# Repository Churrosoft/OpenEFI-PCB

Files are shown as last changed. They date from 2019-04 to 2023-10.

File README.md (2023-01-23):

# OpenEFI-PCB
Coleccion de PCB y planos recomendados para montar una OpenEFI

### Sobre el proyecto
OpenEFI es un ECU/EFI programable basada en arduino, totalmente OpenSource, fue creada originalmente para reemplazar una ecu existente en un motor naftero, pero tambien se puede usar para agregar inyeccion y/o encendido electronico a un motor antiguo, cuenta tambien con soporte para DTC's y autodiagnostico
* [OpenEFI](https://github.com/FDSoftware/OpenEFI) [Repo principal con todo el codigo]
* [OpenEFI-Tuner](https://github.com/FDSoftware/OpenEFI-Tuner) [Utilidad para revisar el estado de la ecu y modificarla]
* 
### Placas soportadas
* STM32F407xxxx: uEFI (v2/v3)
* STM32F103c8t6: OpenEFI (v0.5/v1/v2)

### coautores externos:
Dibujos:
Lucacik / ig: https://www.instagram.com/luca.cik/

si quieres usar otra placa basada en Arduino (Uno, Mega,DUE,etc), puedes hacerlo, pero los pcb no te serviran y capaz tengas que modificar ligeramente el codigo y el mapeo de los pines, proximamente agregare mas pcb ademas de mejorar los existentes

This source is distributed WITHOUT ANY EXPRESS OR IMPLIED WARRANTY, INCLUDING OF MERCHANTABILITY, SATISFACTORY QUALITY AND FITNESS FOR A PARTICULAR PURPOSE.

Please see LICENSE file for applicable conditions.

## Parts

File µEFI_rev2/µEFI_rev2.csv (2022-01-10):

Source: | /home/fdsoftware/repos/churrosoft/OpenEFI-PCB/µEFI_rev2/µEFI_rev2.kicad_sch
Date: | mar 05 oct 2021 17:01:05
Tool: | Eeschema (5.99.0-12387-g847c9e32c8)
Generator: | /usr/share/kicad-nightly/plugins/bom_csv_grouped_by_value.py
Component Count: | 171
Individual Components:
Item | Qty | Reference(s) | Value | LibPart | Footprint | Datasheet | Availability | DIGY | Description | Field4 | Field5 | Field6 | Field7 | Height | LCSC | MF | MP | Manufacturer_Name | Manufacturer_Part_Number | Mouser Part Number | Mouser Price/Stock | Note | Package | Price | STOCK
 |  | C2 | 15pF | Device:C_Small | Capacitor_SMD:C_0805_2012Metric | ~ |  |  |  |  |  |  |  |  | C1794
 |  | C3 | 15pF | Device:C_Small | Capacitor_SMD:C_0805_2012Metric | ~ |  |  |  |  |  |  |  |  | C1794
 |  | C5 | 100nF | Device:C_Small | Capacitor_SMD:C_0805_2012Metric | ~ |  |  |  |  |  |  |  |  | C49678
 |  | C6 | 1uF | Device:C_Small | Capacitor_SMD:C_0805_2012Metric | ~ |  |  |  |  |  |  |  |  | C28323
 |  | C7 | 2.2uF | Device:C_Small | Capacitor_SMD:C_0805_2012Metric | ~ |  |  |  |  |  |  |  |  | C49217 |  |  |  |  |  |  | Low ESR <2Ohm
 |  | C8 | 2.2uF | Device:C_Small | Capacitor_SMD:C_0805_2012Metric | ~ |  |  |  |  |  |  |  |  | C49217 |  |  |  |  |  |  | Low ESR <2Ohm
 |  | C9 | 100nF | Device:C_Small | Capacitor_SMD:C_0805_2012Metric | ~ |  |  |  |  |  |  |  |  | C49678
 |  | C10 | 100nF | Device:C_Small | Capacitor_SMD:C_0805_2012Metric | ~ |  |  |  |  |  |  |  |  | C49678
 |  | C11 | 100nF | Device:C_Small | Capacitor_SMD:C_0805_2012Metric | ~ |  |  |  |  |  |  |  |  | C49678
 |  | C12 | 100nF | Device:C_Small | Capacitor_SMD:C_0805_2012Metric | ~ |  |  |  |  |  |  |  |  | C49678
 |  | C13 | 100nF | Device:C_Small | Capacitor_SMD:C_0805_2012Metric | ~ |  |  |  |  |  |  |  |  | C49678
 |  | C14 | 100nF | Device:C_Small | Capacitor_SMD:C_0805_2012Metric | ~ |  |  |  |  |  |  |  |  | C49678
 |  | C15 | 100nF | Device:C_Small | Capacitor_SMD:C_0805_2012Metric | ~ |  |  |  |  |  |  |  |  | C49678
 |  | C16 | 4.7uF | Device:CP_Small | Capacitor_SMD:C_0805_2012Metric | ~ |  |  |  |  |  |  |  |  | 0805
 |  | C17 | 100nF | Device:C_Small | Capacitor_SMD:C_0805_2012Metric | ~ |  |  |  |  |  |  |  |  | C49678
 |  | C18 | 10pF | Device:C_Small | Capacitor_SMD:C_0603_1608Metric | ~ |  |  |  |  |  |  |  |  | C106245
 |  | C19 | 10pF | Device:C_Small | Capacitor_SMD:C_0603_1608Metric | ~ |  |  |  |  |  |  |  |  | C106245
 |  | C20 | 10pF | Device:C_Small | Capacitor_SMD:C_0603_1608Metric | ~ |  |  |  |  |  |  |  |  | C106245
 |  | C21 | 10pF | Device:C_Small | Capacitor_SMD:C_0603_1608Metric | ~ |  |  |  |  |  |  |  |  | C106245
 |  | C22 | 10pF | Device:C_Small | Capacitor_SMD:C_0603_1608Metric | ~
 |  | C23 | 10nF | Device:C_Small | Capacitor_SMD:C_0603_1608Metric | ~ |  |  |  |  |  |  |  |  | C100042
 |  | C24 | 10nF | Device:C_Small | Capacitor_SMD:C_0603_1608Metric | ~ |  |  |  |  |  |  |  |  | C100042
 |  | C25 | 10nF | Device:C_Small | Capacitor_SMD:C_0603_1608Metric | ~ |  |  |  |  |  |  |  |  | C100042
 |  | C26 | 10nF | Device:C_Small | Capacitor_SMD:C_0603_1608Metric | ~ |  |  |  |  |  |  |  |  | C100042
 |  | C27 | 10nF | Device:C_Small | Capacitor_SMD:C_0603_1608Metric | ~ |  |  |  |  |  |  |  |  | C100042
 |  | C28 | 10nF | Device:C_Small | Capacitor_SMD:C_0603_1608Metric | ~ |  |  |  |  |  |  |  |  | C100042
 |  | C29 | 10nF | Device:C_Small | Capacitor_SMD:C_0603_1608Metric | ~ |  |  |  |  |  |  |  |  | C100042
 |  | C30 | 10nF | Device:C_Small | Capacitor_SMD:C_0603_1608Metric | ~ |  |  |  |  |  |  |  |  | C100042
 |  | C31 | 100uF ±20% 35V | Device:CP_Small | Capacitor_SMD:CP_Elec_6.3x7.7 | ~ |  |  |  |  |  |  |  |  | C141427
 |  | C33 | 47nF | Device:C_Small | Capacitor_SMD:C_0603_1608Metric | ~
 |  | C34 | 4.7nF | Device:C_Small | Capacitor_SMD:C_0805_2012Metric | ~ |  |  |  |  |  |  |  |  | C77475
 |  | C36 | 0.1uF | Device:C_Small | Capacitor_SMD:C_0603_1608Metric | ~
 |  | C49 | 240pF | Device:C_Small | Capacitor_SMD:C_0603_1608Metric | ~ |  |  |  |  |  |  |  |  | C185593
 |  | C51 | 240pF | Device:C_Small | Capacitor_SMD:C_0603_1608Metric | ~ |  |  |  |  |  |  |  |  | C185593
 |  | C52 | 0.01uF | Device:C_Small | Capacitor_SMD:C_0603_1608Metric | ~ |  |  |  |  |  |  |  |  | C100042
 |  | C53 | 0.01uF | Device:C_Small | Capacitor_SMD:C_0603_1608Metric | ~ |  |  |  |  |  |  |  |  | C100042
 |  | C54 | 0.01uF | Device:C_Small | Capacitor_SMD:C_0603_1608Metric | ~ |  |  |  |  |  |  |  |  | C100042
 |  | C55 | 0.01uF | Device:C_Small | Capacitor_SMD:C_0603_1608Metric | ~ |  |  |  |  |  |  |  |  | C100042
 |  | C56 | 0.01uF | Device:C_Small | Capacitor_SMD:C_0603_1608Metric | ~ |  |  |  |  |  |  |  |  | C100042
 |  | C57 | 0.01uF | Device:C_Small | Capacitor_SMD:C_0603_1608Metric | ~ |  |  |  |  |  |  |  |  | C100042
 |  | D1 | LED | Device:LED | LED_SMD:LED_0603_1608Metric | ~
 |  | D2 | 1N4148 | Diode:1N4148 | Diode_SMD:D_SOD-523 | https://assets.nexperia.com/documents/data-sheet/1N4148_1N4448.pdf |  |  |  |  |  |  |  |  | C511874
 |  | D3 | 1N4148 | Diode:1N4148 | Diode_SMD:D_SOD-523 | https://assets.nexperia.com/documents/data-sheet/1N4148_1N4448.pdf |  |  |  |  |  |  |  |  | C511874
 |  | D4 | SMAJ58CA | Device:D_TVS | Diode_SMD:D_SMA | ~
 |  | D5 | LED | Device:LED | LED_SMD:LED_0603_1608Metric | ~
 |  | D6 | LED | Device:LED | LED_SMD:LED_0603_1608Metric | ~
 |  | D7 | LED | Device:LED | LED_SMD:LED_0603_1608Metric | ~
 |  | D8 | LED | Device:LED | LED_SMD:LED_0603_1608Metric | ~
 |  | D9 | LED | Device:LED | LED_SMD:LED_0603_1608Metric | ~
 |  | D10 | LED | Device:LED | LED_SMD:LED_0603_1608Metric | ~
 |  | D11 | MM3Z24VT1G | Device:D_Zener | Diode_SMD:D_SOD-323 | ~ |  |  |  |  |  |  |  |  |  |  |  |  |  |  |  |  |  |  | BI000000597
 |  | D12 | LED | Device:LED | LED_SMD:LED_0603_1608Metric | ~
 |  | D13 | LED | Device:LED | LED_SMD:LED_0603_1608Metric | ~
 |  | D14 | DZ2S033X0L | :Diode:DZ2S033X0L_1 | Diode_SMD:D_MiniMELF | https://industrial.panasonic.com/content/data/SC/ds/ds4/DZ2S03300L_E.pdf |  |  |  |  |  |  |  |  | C8056
 |  | D18 | DZ2S033X0L | Diode:DZ2S033X0L | Diode_SMD:D_MiniMELF | https://industrial.panasonic.com/content/data/SC/ds/ds4/DZ2S03300L_E.pdf |  |  |  |  |  |  |  |  | C8056
 |  | H1 | MountingHole | Mechanical:MountingHole | MountingHole:MountingHole_2.2mm_M2_Pad_Via | ~
 |  | H2 | MountingHole | Mechanical:MountingHole | MountingHole:MountingHole_2.2mm_M2_Pad_Via | ~
 |  | H3 | MountingHole | Mechanical:MountingHole | MountingHole:MountingHole_2.2mm_M2_Pad_Via | ~
 |  | H4 | MountingHole | Mechanical:MountingHole | MountingHole:MountingHole_2.2mm_M2_Pad_Via | ~
 |  | H5 | MountingHole | Mechanical:MountingHole | TestPoint:TestPoint_Pad_D1.0mm | ~
 |  | H6 | MountingHole | Mechanical:MountingHole | TestPoint:TestPoint_Pad_D1.0mm | ~
 |  | H7 | MountingHole | Mechanical:MountingHole | TestPoint:TestPoint_Pad_D1.0mm | ~
 |  | H8 | MountingHole | Mechanical:MountingHole | TestPoint:TestPoint_Pad_D1.0mm | ~
 |  | H9 | MountingHole | Mechanical:MountingHole | MountingHole:MountingHole_2.2mm_M2_Pad_Via | ~
 |  | J1 | USB_B | STM32F_rev3-rescue:USB_B-Connector | Connector_USB:USB_B_OST_USB-B1HSxx_Horizontal | ~
 |  | J2 | Tag connect | Connector_Generic:Conn_02x03_Odd_Even | Connector:Tag-Connect_TC2030-IDC-NL_2x03_P1.27mm_Vertical | ~
 |  | J3 | 36638-0002 | OpenEFI-STM32-rev3:36638-0002 | 366380002 | https://www.molex.com/webdocs/datasheets/pdf/en-us/0366380002_PCB_HEADERS.pdf |  |  | MOLEX - 36638-0002 - HEADER, CMC, SINGLE PORT, R/A, 48WAY |  |  |  |  | 30 |  |  |  | Molex | 36638-0002 | 538-36638-0002 | https://www.mouser.co.uk/ProductDetail/Molex/36638-0002?qs=xXuHO2M8Escly3rEMcmzyw%3D%3D
 |  | J4 | Conn_02x08_Odd_Even | Connector_Generic:Conn_02x08_Odd_Even | Connector_PinHeader_1.27mm:PinHeader_2x08_P1.27mm_Vertical | ~
 |  | JP1 | SolderJumper_2_Open | Jumper:SolderJumper_2_Open | Jumper:SolderJumper-2_P1.3mm_Open_RoundedPad1.0x1.5mm | ~
 |  | JP2 | SolderJumper_2_Open | Jumper:SolderJumper_2_Open | Jumper:SolderJumper-2_P1.3mm_Open_RoundedPad1.0x1.5mm | ~
 |  | JP3 | SolderJumper_2_Open | Jumper:SolderJumper_2_Open | Jumper:SolderJumper-2_P1.3mm_Open_RoundedPad1.0x1.5mm | ~
 |  | JP4 | Jumper_NO_Small | Device:Jumper_NO_Small | Jumper:SolderJumper-2_P1.3mm_Open_RoundedPad1.0x1.5mm | ~
 |  | JP11 | Jumper_NC_Small | Device:Jumper_NC_Small | Jumper:SolderJumper-2_P1.3mm_Open_TrianglePad1.0x1.5mm | ~
 |  | JP15 | Jumper_NC_Small | Device:Jumper_NC_Small | Jumper:SolderJumper-2_P1.3mm_Open_TrianglePad1.0x1.5mm | ~
 |  | JP17 | Jumper_NC_Small | Device:Jumper_NC_Small | Jumper:SolderJumper-2_P1.3mm_Open_TrianglePad1.0x1.5mm | ~
 |  | JP18 | Jumper_NC_Small | Device:Jumper_NC_Small | Jumper:SolderJumper-2_P1.3mm_Open_TrianglePad1.0x1.5mm | ~
 |  | JP19 | Jumper_NC_Small | Device:Jumper_NC_Small | Jumper:SolderJumper-2_P1.3mm_Open_TrianglePad1.0x1.5mm | ~
 |  | JP23 | SolderJumper_2_Open | Jumper:SolderJumper_2_Open | Jumper:SolderJumper-2_P1.3mm_Open_RoundedPad1.0x1.5mm | ~
 |  | JP24 | SolderJumper_2_Open | Jumper:SolderJumper_2_Open | Jumper:SolderJumper-2_P1.3mm_Open_RoundedPad1.0x1.5mm | ~
 |  | LOGO1 | Logo_Open_Hardware_Large | Graphic:Logo_Open_Hardware_Large | Symbol:OSHW-Logo2_14.6x12mm_SilkScreen | ~
 |  | Q1 | ISL9V5045S3ST | Device:Q_NIGBT_GCE | Package_TO_SOT_SMD:TO-263-2 | ~
 |  | Q2 | ISL9V5045S3ST | Device:Q_NIGBT_GCE | Package_TO_SOT_SMD:TO-263-2 | ~
 |  | Q3 | ISL9V5045S3ST | Device:Q_NIGBT_GCE | Package_TO_SOT_SMD:TO-263-2 | ~
 |  | Q4 | ISL9V5045S3ST | Device:Q_NIGBT_GCE | Package_TO_SOT_SMD:TO-263-2 | ~
 |  | Q5 | SS8050 | Transistor_BJT:2N3055 | Package_TO_SOT_SMD:SOT-23 | http://www.onsemi.com/pub_link/Collateral/2N3055-D.PDF |  |  |  |  |  |  |  |  | C2150
 |  | Q6 | IRF540N | :Transistor_FET:IRF540N_1 | Package_TO_SOT_THT:TO-220-3_Vertical | http://www.irf.com/product-info/datasheets/data/irf540n.pdf
 |  | Q7 | IRF540N | :Transistor_FET:IRF540N_2 | Package_TO_SOT_THT:TO-220-3_Vertical | http://www.irf.com/product-info/datasheets/data/irf540n.pdf
 |  | Q8 | SS8050 | Transistor_BJT:2N3055 | Package_TO_SOT_SMD:SOT-23 | http://www.onsemi.com/pub_link/Collateral/2N3055-D.PDF |  |  |  |  |  |  |  |  | C2150
 |  | Q9 | SS8050 | Transistor_BJT:2N3055 | Package_TO_SOT_SMD:SOT-23 | http://www.onsemi.com/pub_link/Collateral/2N3055-D.PDF |  |  |  |  |  |  |  |  | C2150
 |  | Q10 | IRF540N | Transistor_FET:IRF540N | Package_TO_SOT_THT:TO-220-3_Vertical | http://www.irf.com/product-info/datasheets/data/irf540n.pdf
 |  | Q11 | SS8050 | Transistor_BJT:2N3055 | Package_TO_SOT_SMD:SOT-23 | http://www.onsemi.com/pub_link/Collateral/2N3055-D.PDF |  |  |  |  |  |  |  |  | C2150
 |  | Q12 | AO3400A | Transistor_FET:AO3400A | Package_TO_SOT_SMD:SOT-23 | http://www.aosmd.com/pdfs/datasheet/AO3400A.pdf |  |  |  |  |  |  |  |  | C347475
 |  | R1 | R_Small | Device:R_Small | Resistor_SMD:R_1206_3216Metric | ~ |  |  |  |  |  |  |  |  | C205298
 |  | R2 | 10k | Device:R_Small | Resistor_SMD:R_0603_1608Metric | ~
 |  | R3 | 4.7k | Device:R_Small | Resistor_SMD:R_0603_1608Metric | ~ |  |  |  |  |  |  |  |  | C23162
 |  | R4 | 4.7k | Device:R_Small | Resistor_SMD:R_0603_1608Metric | ~ |  |  |  |  |  |  |  |  | C23162
 |  | R5 | 4.7k | Device:R_Small | Resistor_SMD:R_0603_1608Metric | ~ |  |  |  |  |  |  |  |  | C23162
 |  | R6 | 100R | Device:R_Small | Resistor_SMD:R_0603_1608Metric | ~ |  |  |  |  |  |  |  |  | C159890
 |  | R7 | 100R | Device:R_Small | Resistor_SMD:R_0603_1608Metric | ~ |  |  |  |  |  |  |  |  | C159890
 |  | R8 | 0.02R | Device:R_Small | Resistor_SMD:R_2512_6332Metric | ~ |  |  |  |  |  |  |  |  | C326611
 |  | R9 | 4.02k | Device:R_Small | Resistor_SMD:R_0603_1608Metric | ~ |  |  |  |  |  |  |  |  | C23040
 |  | R10 | 4.02k | Device:R_Small | Resistor_SMD:R_0603_1608Metric | ~ |  |  |  |  |  |  |  |  | C23040
 |  | R11 | 4.02k | Device:R_Small | Resistor_SMD:R_0603_1608Metric | ~ |  |  |  |  |  |  |  |  | C23040
 |  | R12 | 4.02k | Device:R_Small | Resistor_SMD:R_0603_1608Metric | ~ |  |  |  |  |  |  |  |  | C23040
 |  | R13 | 36K | Device:R_Small | Resistor_SMD:R_0603_1608Metric | ~ |  |  |  |  |  |  |  |  | C192548
 |  | R14 | 36K | Device:R_Small | Resistor_SMD:R_0603_1608Metric | ~ |  |  |  |  |  |  |  |  | C192548
 |  | R15 | 36K | Device:R_Small | Resistor_SMD:R_0603_1608Metric | ~ |  |  |  |  |  |  |  |  | C192548
 |  | R16 | 36K | Device:R_Small | Resistor_SMD:R_0603_1608Metric | ~ |  |  |  |  |  |  |  |  | C192548
 |  | R17 | 10K 1/10W | Device:R_Small | Resistor_SMD:R_0603_1608Metric | ~
 |  | R18 | 10R 1/10W | Device:R_Small | Resistor_SMD:R_0603_1608Metric | ~
 |  | R19 | 1M 1/10W | Device:R_Small | Resistor_SMD:R_0603_1608Metric | ~
 |  | R20 | 10R 1/10W | Device:R_Small | Resistor_SMD:R_0603_1608Metric | ~
 |  | R21 | 0.01R | Device:R_Small | Resistor_SMD:R_1210_3225Metric | ~ |  |  |  |  |  |  |  |  | C175884
 |  | R22 | 57.6K 1/10W | Device:R_Small | Resistor_SMD:R_0603_1608Metric | ~
 |  | R23 | 4.99K 1/10W | Device:R_Small | Resistor_SMD:R_0603_1608Metric | ~
 |  | R24 | 4.7k | Device:R_Small | Resistor_SMD:R_0603_1608Metric | ~ |  |  |  |  |  |  |  |  | C23162
 |  | R25 | 4.7k | Device:R_Small | Resistor_SMD:R_0603_1608Metric | ~ |  |  |  |  |  |  |  |  | C23162
 |  | R26 | 4.7k | Device:R_Small | Resistor_SMD:R_0603_1608Metric | ~ |  |  |  |  |  |  |  |  | C23162
 |  | R27 | 4.7k | Device:R_Small | Resistor_SMD:R_0603_1608Metric | ~ |  |  |  |  |  |  |  |  | C23162
 |  | R28 | R_Small | Device:R_Small | Resistor_SMD:R_1206_3216Metric | ~ |  |  |  |  |  |  |  |  | C205298
 |  | R29 | 4.7k | Device:R_Small | Resistor_SMD:R_0603_1608Metric | ~ |  |  |  |  |  |  |  |  | C23162
 |  | R30 | 4.7k | Device:R_Small | Resistor_SMD:R_0603_1608Metric | ~ |  |  |  |  |  |  |  |  | C23162
 |  | R31 | 1k | Device:R | Resistor_SMD:R_0603_1608Metric | ~ |  |  |  |  |  |  |  |  | C21190
 |  | R32 | 1k | Device:R | Resistor_SMD:R_0603_1608Metric | ~ |  |  |  |  |  |  |  |  | C21190
 |  | R33 | 10R 1/10W | Device:R_Small | Resistor_SMD:R_0603_1608Metric | ~
 |  | R34 | 1k | Device:R | Resistor_SMD:R_0603_1608Metric | ~ |  |  |  |  |  |  |  |  | C21190
 |  | R35 | 100k | Device:R | Resistor_SMD:R_0805_2012Metric | ~ |  |  |  |  |  |  |  |  | --- |  |  |  |  |  |  |  |  |  | 44
 |  | R81 | 4.99K 1/2W | Device:R_Small | Resistor_SMD:R_1210_3225Metric | ~ |  |  |  |  |  |  |  |  | C407178
 |  | R82 | 100k 1/10W +-1% | Device:R_Small | Resistor_SMD:R_0603_1608Metric | ~ |  |  |  |  |  |  |  |  | C217840
 |  | R83 | 20k 1/10W +-1% | Device:R_Small | Resistor_SMD:R_0603_1608Metric | ~
 |  | R87 | 3.32k +-1% | Device:R_Small | Resistor_SMD:R_0603_1608Metric | ~ |  |  |  |  |  |  |  |  | C234508
 |  | R92 | 28.6k +-1% | Device:R_Small | Resistor_SMD:R_0603_1608Metric | ~ |  |  |  |  |  |  |  |  | C217931
 |  | R97 | 2.2k | Device:R_Small | Resistor_SMD:R_0603_1608Metric | ~ |  |  |  |  |  |  |  |  | C309092
 |  | R108 | 10k | Device:R_Small | Resistor_SMD:R_0603_1608Metric | ~
 |  | R109 | 10k | Device:R_Small | Resistor_SMD:R_0603_1608Metric | ~
 |  | R112 | 4.99K 1/2W | Device:R_Small | Resistor_SMD:R_1210_3225Metric | ~ |  |  |  |  |  |  |  |  | C407178
 |  | R113 | 4.99K 1/2W | Device:R_Small | Resistor_SMD:R_1210_3225Metric | ~ |  |  |  |  |  |  |  |  | C407178
 |  | R114 | 4.99K 1/2W | Device:R_Small | Resistor_SMD:R_1210_3225Metric | ~ |  |  |  |  |  |  |  |  | C407178
 |  | R115 | 4.99K 1/2W | Device:R_Small | Resistor_SMD:R_1210_3225Metric | ~ |  |  |  |  |  |  |  |  | C407178
 |  | R116 | 4.99K 1/2W | Device:R_Small | Resistor_SMD:R_1210_3225Metric | ~ |  |  |  |  |  |  |  |  | C407178
 |  | R117 | 4.99K 1/2W | Device:R_Small | Resistor_SMD:R_1210_3225Metric | ~ |  |  |  |  |  |  |  |  | C407178
 |  | R118 | 4.99K 1/2W | Device:R_Small | Resistor_SMD:R_1210_3225Metric | ~ |  |  |  |  |  |  |  |  | C407178
 |  | R119 | 4.99K 1/2W | Device:R_Small | Resistor_SMD:R_1210_3225Metric | ~ |  |  |  |  |  |  |  |  | C407178
 |  | R120 | 4.99K 1/2W | Device:R_Small | Resistor_SMD:R_1210_3225Metric | ~ |  |  |  |  |  |  |  |  | C407178
 |  | R121 | R_Small | Device:R_Small | Resistor_SMD:R_0603_1608Metric | ~
 |  | R122 | R_Small | Device:R_Small | Resistor_SMD:R_0603_1608Metric | ~
 |  | SW1 | SW_Push | Switch:SW_Push | Button_Switch_SMD:SW_SPST_TL3342 | ~
 |  | SYM1 | SYM_Hot_Small | Graphic:SYM_Hot_Small | Symbol:KiCad-Logo2_6mm_SilkScreen | ~
 |  | SYM111 | SYM_Hot_Large | Graphic:SYM_Hot_Large | OpenEFI-STM32F_rev3:churro_new_v4 | ~
 |  | U1 | MCZ33810EK | OpenEFI-STM32-rev3:MCZ33810EK | SOP65P1030X245-33N | - |  |  |  | FREESCALE SEMICONDUCTOR | 45P4988 | SOP-32 | MCZ33810EK
 |  | U2 | SensorsV2 | :OpenEFI-STM32-rev3:SensorsV2_5 | OpenEFI-STM32F_rev3:Sensors_v2
 |  | U3 | STM32F407VGTx | MCU_ST_STM32F4:STM32F407VGTx | Package_QFP:LQFP-100_14x14mm_P0.5mm | http://www.st.com/st-web-ui/static/active/en/resource/technical/document/datasheet/DM00037051.pdf
 |  | U4 | MIC2940A-3.3WU | Regulator_Linear:L7805 | Package_TO_SOT_SMD:TO-263-3_TabPin2 | http://www.st.com/content/ccc/resource/technical/document/datasheet/41/4f/b3/b0/12/d4/47/88/CD00000444.pdf/files/CD00000444.pdf/jcr:content/translations/en.CD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
 |  | U5 | MIC2940A-5.0WT | Regulator_Linear:L7805 | Package_TO_SOT_THT:TO-220-3_Vertical | http://www.st.com/content/ccc/resource/technical/document/datasheet/41/4f/b3/b0/12/d4/47/88/CD00000444.pdf/files/CD00000444.pdf/jcr:content/translations/en.CD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 |  | 576-1136-ND
 |  | U6 | LT4363IMS | OpenEFI-STM32-rev3:LT4363IMS | Package_SO:SOIC-16W_7.5x10.3mm_P1.27mm | https://ar.mouser.com/datasheet/2/609/ADuM4160-1503590.pdf
 |  | U7 | 25LCxxx | Memory_EEPROM:25LCxxx | Package_SO:SOIC-8_3.9x4.9mm_P1.27mm | http://ww1.microchip.com/downloads/en/DeviceDoc/21832H.pdf
 |  | U8 | SensorsV2 | :OpenEFI-STM32-rev3:SensorsV2_2 | OpenEFI-STM32F_rev3:Sensors_v2
 |  | U9 | SensorsV2 | :OpenEFI-STM32-rev3:SensorsV2_1 | OpenEFI-STM32F_rev3:Sensors_v2
 |  | U10 | SensorsV2 | :OpenEFI-STM32-rev3:SensorsV2_4 | OpenEFI-STM32F_rev3:Sensors_v2
 |  | U11 | SensorsV2 | :OpenEFI-STM32-rev3:SensorsV2_7 | OpenEFI-STM32F_rev3:Sensors_v2
 |  | U12 | SensorsV2 | :OpenEFI-STM32-rev3:SensorsV2_3 | OpenEFI-STM32F_rev3:Sensors_v2
 |  | U13 | SensorsV2 | :OpenEFI-STM32-rev3:SensorsV2_6 | OpenEFI-STM32F_rev3:Sensors_v2
 |  | U14 | SensorsV2 | OpenEFI-STM32-rev3:SensorsV2 | OpenEFI-STM32F_rev3:Sensors_v2
 |  | U15 | TJA1042T3118 | OpenEFI-STM32-rev3:TJA1042T3118 | Package_SO:HTSOP-8-1EP_3.9x4.9mm_P1.27mm_EP2.4x3.2mm
 |  | U20 | TPL7407LAPWR | OpenEFI-STM32-rev3:TPL7407LAPWR | Package_SO:TSSOP-16_4.4x5mm_P0.65mm
 |  | U22 | TPL7407LAPWR | OpenEFI-STM32-rev3:TPL7407LAPWR | Package_SO:TSSOP-16_4.4x5mm_P0.65mm
 |  | U23 | PaP_Driver_v1 | OpenEFI-STM32-rev3:PaP_Driver_v1 | OpenEFI-STM32F_rev3:DIP-16_598_ELL
 |  | U27 | LM321 | Amplifier_Operational:LM321 | Package_TO_SOT_SMD:SOT-23-5 | http://www.ti.com/lit/ds/symlink/lm321.pdf
 |  | U31 | LM321 | Amplifier_Operational:LM321 | Package_TO_SOT_SMD:SOT-23-5 | http://www.ti.com/lit/ds/symlink/lm321.pdf
 |  | U36 | MAX9926UAEE+ | OpenEFI-STM32-rev3:MAX9926UAEE+ | OpenEFI-STM32F_rev3:SOP63P602X175-16N |  | Unavailable |  | Variable Reluctance Sensor Interface 16-Pin QSOP Tube |  |  |  |  |  |  | Maxim Integrated | MAX9926UAEE+ |  |  |  |  |  | QSOP-16 Maxim | None
 |  | Y1 | 25MHz | Device:Crystal_GND24 | Crystal:Crystal_SMD_3225-4Pin_3.2x2.5mm | ~
Collated Components:
Item | Qty | Reference(s) | Value | LibPart | Footprint | Datasheet | Availability | DIGY | Description | Field4 | Field5 | Field6 | Field7 | Height | LCSC | MF | MP | Manufacturer_Name | Manufacturer_Part_Number | Mouser Part Number | Mouser Price/Stock | Note | Package | Price | STOCK
1 | 2 | C2, C3 | 15pF | Device:C_Small | Capacitor_SMD:C_0805_2012Metric | ~ |  |  |  |  |  |  |  |  | C1794
2 | 9 | C5, C9, C10, C11, C12, C13, C14, C15, C17 | 100nF | Device:C_Small | Capacitor_SMD:C_0805_2012Metric | ~ |  |  |  |  |  |  |  |  | C49678
3 | 1 | C6 | 1uF | Device:C_Small | Capacitor_SMD:C_0805_2012Metric | ~ |  |  |  |  |  |  |  |  | C28323
4 | 2 | C7, C8 | 2.2uF | Device:C_Small | Capacitor_SMD:C_0805_2012Metric | ~ |  |  |  |  |  |  |  |  | C49217 |  |  |  |  |  |  | Low ESR <2Ohm
5 | 1 | C16 | 4.7uF | Device:CP_Small | Capacitor_SMD:C_0805_2012Metric | ~ |  |  |  |  |  |  |  |  | 0805
6 | 5 | C18, C19, C20, C21, C22 | 10pF | Device:C_Small | Capacitor_SMD:C_0603_1608Metric | ~ |  |  |  |  |  |  |  |  | C106245
7 | 8 | C23, C24, C25, C26, C27, C28, C29, C30 | 10nF | Device:C_Small | Capacitor_SMD:C_0603_1608Metric | ~ |  |  |  |  |  |  |  |  | C100042
8 | 1 | C31 | 100uF ±20% 35V | Device:CP_Small | Capacitor_SMD:CP_Elec_6.3x7.7 | ~ |  |  |  |  |  |  |  |  | C141427
9 | 1 | C33 | 47nF | Device:C_Small | Capacitor_SMD:C_0603_1608Metric | ~
10 | 1 | C34 | 4.7nF | Device:C_Small | Capacitor_SMD:C_0805_2012Metric | ~ |  |  |  |  |  |  |  |  | C77475
11 | 1 | C36 | 0.1uF | Device:C_Small | Capacitor_SMD:C_0603_1608Metric | ~
12 | 2 | C49, C51 | 240pF | Device:C_Small | Capacitor_SMD:C_0603_1608Metric | ~ |  |  |  |  |  |  |  |  | C185593
13 | 6 | C52, C53, C54, C55, C56, C57 | 0.01uF | Device:C_Small | Capacitor_SMD:C_0603_1608Metric | ~ |  |  |  |  |  |  |  |  | C100042
14 | 9 | D1, D5, D6, D7, D8, D9, D10, D12, D13 | LED | Device:LED | LED_SMD:LED_0603_1608Metric | ~
15 | 2 | D2, D3 | 1N4148 | Diode:1N4148 | Diode_SMD:D_SOD-523 | https://assets.nexperia.com/documents/data-sheet/1N4148_1N4448.pdf |  |  |  |  |  |  |  |  | C511874
16 | 1 | D4 | SMAJ58CA | Device:D_TVS | Diode_SMD:D_SMA | ~
17 | 1 | D11 | MM3Z24VT1G | Device:D_Zener | Diode_SMD:D_SOD-323 | ~ |  |  |  |  |  |  |  |  |  |  |  |  |  |  |  |  |  |  | BI000000597
18 | 1 | D14 | DZ2S033X0L | :Diode:DZ2S033X0L_1 | Diode_SMD:D_MiniMELF | https://industrial.panasonic.com/content/data/SC/ds/ds4/DZ2S03300L_E.pdf |  |  |  |  |  |  |  |  | C8056
19 | 1 | D18 | DZ2S033X0L | Diode:DZ2S033X0L | Diode_SMD:D_MiniMELF | https://industrial.panasonic.com/content/data/SC/ds/ds4/DZ2S03300L_E.pdf |  |  |  |  |  |  |  |  | C8056
20 | 5 | H1, H2, H3, H4, H9 | MountingHole | Mechanical:MountingHole | MountingHole:MountingHole_2.2mm_M2_Pad_Via | ~
21 | 4 | H5, H6, H7, H8 | MountingHole | Mechanical:MountingHole | TestPoint:TestPoint_Pad_D1.0mm | ~
22 | 1 | J1 | USB_B | STM32F_rev3-rescue:USB_B-Connector | Connector_USB:USB_B_OST_USB-B1HSxx_Horizontal | ~
23 | 1 | J2 | Tag connect | Connector_Generic:Conn_02x03_Odd_Even | Connector:Tag-Connect_TC2030-IDC-NL_2x03_P1.27mm_Vertical | ~
24 | 1 | J3 | 36638-0002 | OpenEFI-STM32-rev3:36638-0002 | 366380002 | https://www.molex.com/webdocs/datasheets/pdf/en-us/0366380002_PCB_HEADERS.pdf |  |  | MOLEX - 36638-0002 - HEADER, CMC, SINGLE PORT, R/A, 48WAY |  |  |  |  | 30 |  |  |  | Molex | 36638-0002 | 538-36638-0002 | https://www.mouser.co.uk/ProductDetail/Molex/36638-0002?qs=xXuHO2M8Escly3rEMcmzyw%3D%3D
25 | 1 | J4 | Conn_02x08_Odd_Even | Connector_Generic:Conn_02x08_Odd_Even | Connector_PinHeader_1.27mm:PinHeader_2x08_P1.27mm_Vertical | ~
26 | 5 | JP1, JP2, JP3, JP23, JP24 | SolderJumper_2_Open | Jumper:SolderJumper_2_Open | Jumper:SolderJumper-2_P1.3mm_Open_RoundedPad1.0x1.5mm | ~
27 | 1 | JP4 | Jumper_NO_Small | Device:Jumper_NO_Small | Jumper:SolderJumper-2_P1.3mm_Open_RoundedPad1.0x1.5mm | ~
28 | 5 | JP11, JP15, JP17, JP18, JP19 | Jumper_NC_Small | Device:Jumper_NC_Small | Jumper:SolderJumper-2_P1.3mm_Open_TrianglePad1.0x1.5mm | ~
29 | 1 | LOGO1 | Logo_Open_Hardware_Large | Graphic:Logo_Open_Hardware_Large | Symbol:OSHW-Logo2_14.6x12mm_SilkScreen | ~
30 | 4 | Q1, Q2, Q3, Q4 | ISL9V5045S3ST | Device:Q_NIGBT_GCE | Package_TO_SOT_SMD:TO-263-2 | ~
31 | 4 | Q5, Q8, Q9, Q11 | SS8050 | Transistor_BJT:2N3055 | Package_TO_SOT_SMD:SOT-23 | http://www.onsemi.com/pub_link/Collateral/2N3055-D.PDF |  |  |  |  |  |  |  |  | C2150
32 | 1 | Q6 | IRF540N | :Transistor_FET:IRF540N_1 | Package_TO_SOT_THT:TO-220-3_Vertical | http://www.irf.com/product-info/datasheets/data/irf540n.pdf
33 | 1 | Q7 | IRF540N | :Transistor_FET:IRF540N_2 | Package_TO_SOT_THT:TO-220-3_Vertical | http://www.irf.com/product-info/datasheets/data/irf540n.pdf
34 | 1 | Q10 | IRF540N | Transistor_FET:IRF540N | Package_TO_SOT_THT:TO-220-3_Vertical | http://www.irf.com/product-info/datasheets/data/irf540n.pdf
35 | 1 | Q12 | AO3400A | Transistor_FET:AO3400A | Package_TO_SOT_SMD:SOT-23 | http://www.aosmd.com/pdfs/datasheet/AO3400A.pdf |  |  |  |  |  |  |  |  | C347475
36 | 2 | R1, R28 | R_Small | Device:R_Small | Resistor_SMD:R_1206_3216Metric | ~ |  |  |  |  |  |  |  |  | C205298
37 | 3 | R2, R108, R109 | 10k | Device:R_Small | Resistor_SMD:R_0603_1608Metric | ~
38 | 9 | R3, R4, R5, R24, R25, R26, R27, R29, R30 | 4.7k | Device:R_Small | Resistor_SMD:R_0603_1608Metric | ~ |  |  |  |  |  |  |  |  | C23162
39 | 2 | R6, R7 | 100R | Device:R_Small | Resistor_SMD:R_0603_1608Metric | ~ |  |  |  |  |  |  |  |  | C159890
40 | 1 | R8 | 0.02R | Device:R_Small | Resistor_SMD:R_2512_6332Metric | ~ |  |  |  |  |  |  |  |  | C326611
41 | 4 | R9, R10, R11, R12 | 4.02k | Device:R_Small | Resistor_SMD:R_0603_1608Metric | ~ |  |  |  |  |  |  |  |  | C23040
42 | 4 | R13, R14, R15, R16 | 36K | Device:R_Small | Resistor_SMD:R_0603_1608Metric | ~ |  |  |  |  |  |  |  |  | C192548
43 | 1 | R17 | 10K 1/10W | Device:R_Small | Resistor_SMD:R_0603_1608Metric | ~
44 | 3 | R18, R20, R33 | 10R 1/10W | Device:R_Small | Resistor_SMD:R_0603_1608Metric | ~
45 | 1 | R19 | 1M 1/10W | Device:R_Small | Resistor_SMD:R_0603_1608Metric | ~
46 | 1 | R21 | 0.01R | Device:R_Small | Resistor_SMD:R_1210_3225Metric | ~ |  |  |  |  |  |  |  |  | C175884
47 | 1 | R22 | 57.6K 1/10W | Device:R_Small | Resistor_SMD:R_0603_1608Metric | ~
48 | 1 | R23 | 4.99K 1/10W | Device:R_Small | Resistor_SMD:R_0603_1608Metric | ~
49 | 3 | R31, R32, R34 | 1k | Device:R | Resistor_SMD:R_0603_1608Metric | ~ |  |  |  |  |  |  |  |  | C21190
50 | 1 | R35 | 100k | Device:R | Resistor_SMD:R_0805_2012Metric | ~ |  |  |  |  |  |  |  |  | --- |  |  |  |  |  |  |  |  |  | 44
51 | 10 | R81, R112, R113, R114, R115, R116, R117, R118, R119, R120 | 4.99K 1/2W | Device:R_Small | Resistor_SMD:R_1210_3225Metric | ~ |  |  |  |  |  |  |  |  | C407178
52 | 1 | R82 | 100k 1/10W +-1% | Device:R_Small | Resistor_SMD:R_0603_1608Metric | ~ |  |  |  |  |  |  |  |  | C217840
53 | 1 | R83 | 20k 1/10W +-1% | Device:R_Small | Resistor_SMD:R_0603_1608Metric | ~
54 | 1 | R87 | 3.32k +-1% | Device:R_Small | Resistor_SMD:R_0603_1608Metric | ~ |  |  |  |  |  |  |  |  | C234508
55 | 1 | R92 | 28.6k +-1% | Device:R_Small | Resistor_SMD:R_0603_1608Metric | ~ |  |  |  |  |  |  |  |  | C217931
56 | 1 | R97 | 2.2k | Device:R_Small | Resistor_SMD:R_0603_1608Metric | ~ |  |  |  |  |  |  |  |  | C309092
57 | 2 | R121, R122 | R_Small | Device:R_Small | Resistor_SMD:R_0603_1608Metric | ~
58 | 1 | SW1 | SW_Push | Switch:SW_Push | Button_Switch_SMD:SW_SPST_TL3342 | ~
59 | 1 | SYM1 | SYM_Hot_Small | Graphic:SYM_Hot_Small | Symbol:KiCad-Logo2_6mm_SilkScreen | ~
60 | 1 | SYM111 | SYM_Hot_Large | Graphic:SYM_Hot_Large | OpenEFI-STM32F_rev3:churro_new_v4 | ~
61 | 1 | U1 | MCZ33810EK | OpenEFI-STM32-rev3:MCZ33810EK | SOP65P1030X245-33N | - |  |  |  | FREESCALE SEMICONDUCTOR | 45P4988 | SOP-32 | MCZ33810EK

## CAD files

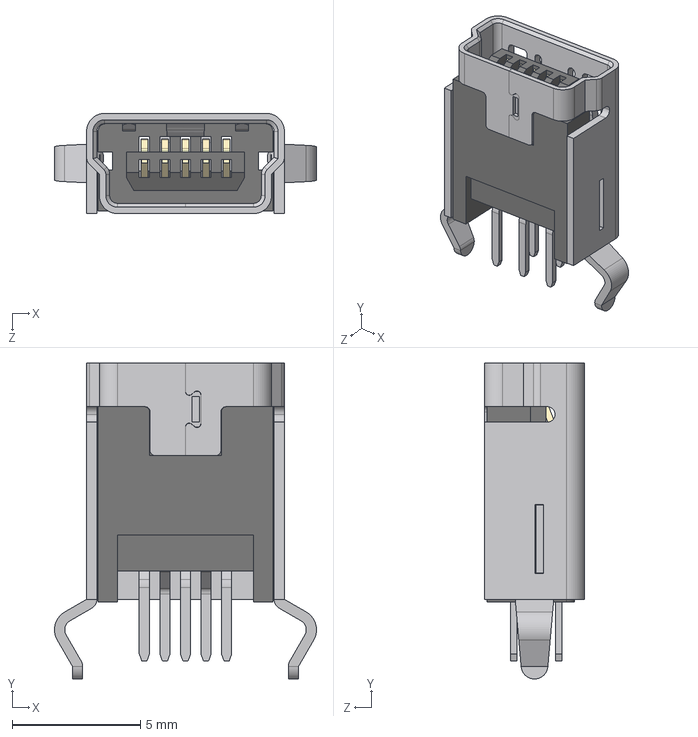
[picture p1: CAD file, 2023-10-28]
OpenEFI_rev4/lib_v4/54-00025--3DModel-STEP-510211.STEP
10.2 x 12.3 x 3.90 mm

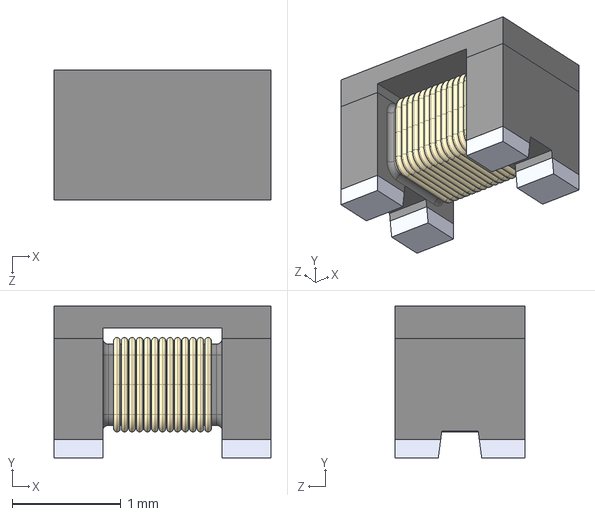
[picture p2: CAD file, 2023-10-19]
OpenEFI_rev4/lib_v4/DLW21SZ900HQ2L.step
2.00 x 1.40 x 1.20 mm

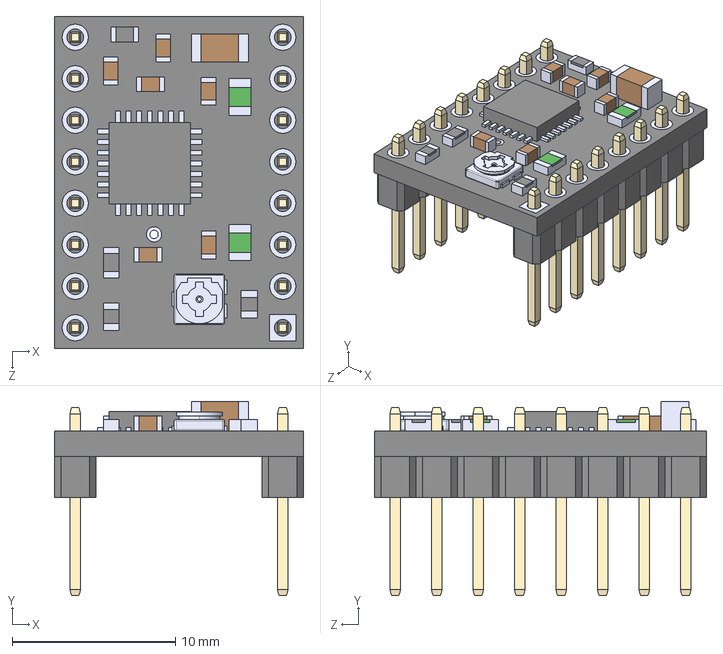
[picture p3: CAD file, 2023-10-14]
OpenEFI_rev4/lib_v4/A4988_STEPPER_MOTOR_DRIVER_CARRIER.step
15.2 x 11.9 x 20.3 mm

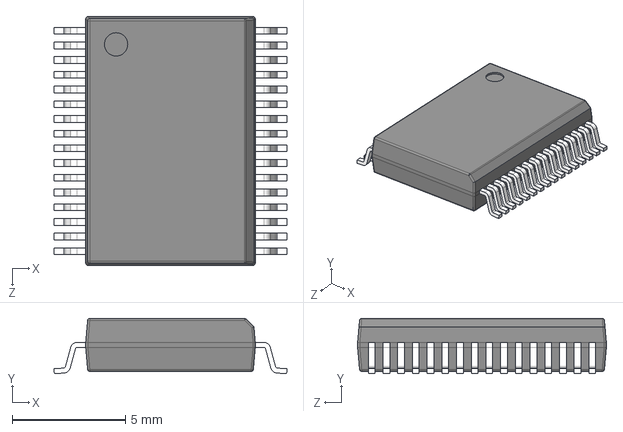
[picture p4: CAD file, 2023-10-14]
OpenEFI_rev4/lib_v4/SOP65P1030X245-33N.step
10.3 x 2.45 x 11.0 mm

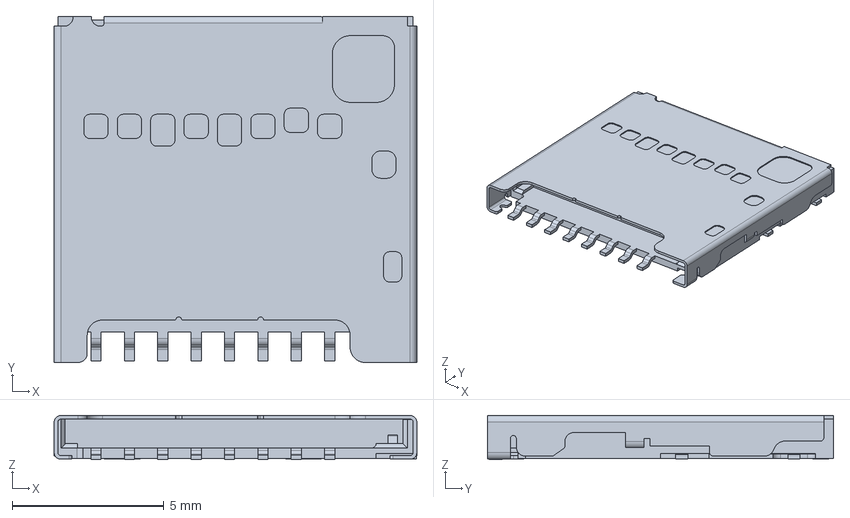
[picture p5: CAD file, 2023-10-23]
OpenEFI_rev4/lib_v4/104031-0811.step
11.9 x 11.4 x 1.45 mm

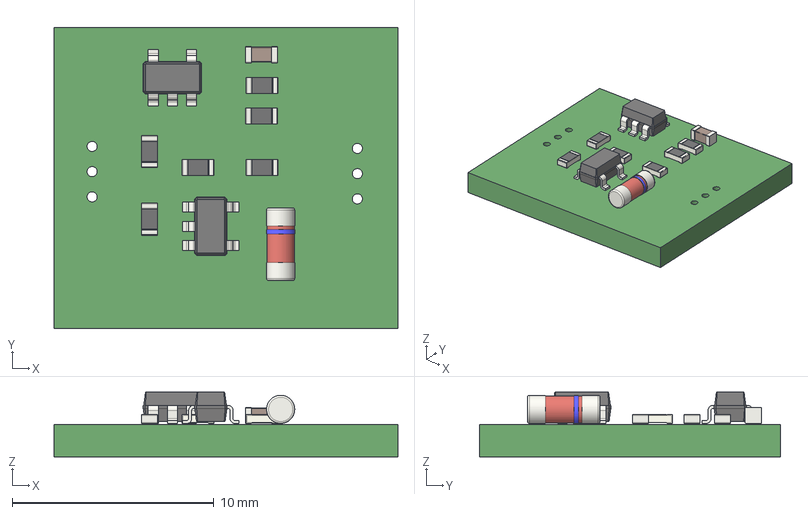
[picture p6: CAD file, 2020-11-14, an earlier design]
OpenEFI_rev4/modules/sensors/v1/SensorsV1.step
17.1 x 14.9 x 3.20 mm

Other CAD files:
cases/uEFI_v3.FCStd

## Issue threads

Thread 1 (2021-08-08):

[SPI] PMIC-FLASH

FDSoftware, 2021-08-08:
Lista de mierdas a arreglar:

- [x] Pines debug para el SPI cerca de la memoria

- [x] doble footprint para las memorias SPI ( DIL-8 / SOIC-8 )

- [x] Conectar bien WP/HOLD

Closed 2022-03-30.

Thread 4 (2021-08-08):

[POWER] Agregar mas protecciones en salidas de voltaje

FDSoftware, 2021-08-08:
Actualmente todo el rail de 5v de los sensores comparte el mismo LDO que el resto de la ecu, solo que pasa por un mosfet para activar el modo de bajo consumo, agregar protecciones de corto/sobreconsumo (max 1A toda la linea)

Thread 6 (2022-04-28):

rev 3 => rev4 issues

FDSoftware, 2022-04-28:
- [ ] U36 R121/R122 5v => 3v source
- [ ] C27/C28/C29/C30 fix orientation
- [ ] Q3/Q4 feedback sensor

FDSoftware, 2022-05-01:
sw regulators:
MAX25223ATPA/VY+ => 5v 3.5A
MAX17626 => 3V 2A (entrada hasta 5.5v nomas)
A8591 => 5V/3V 2A

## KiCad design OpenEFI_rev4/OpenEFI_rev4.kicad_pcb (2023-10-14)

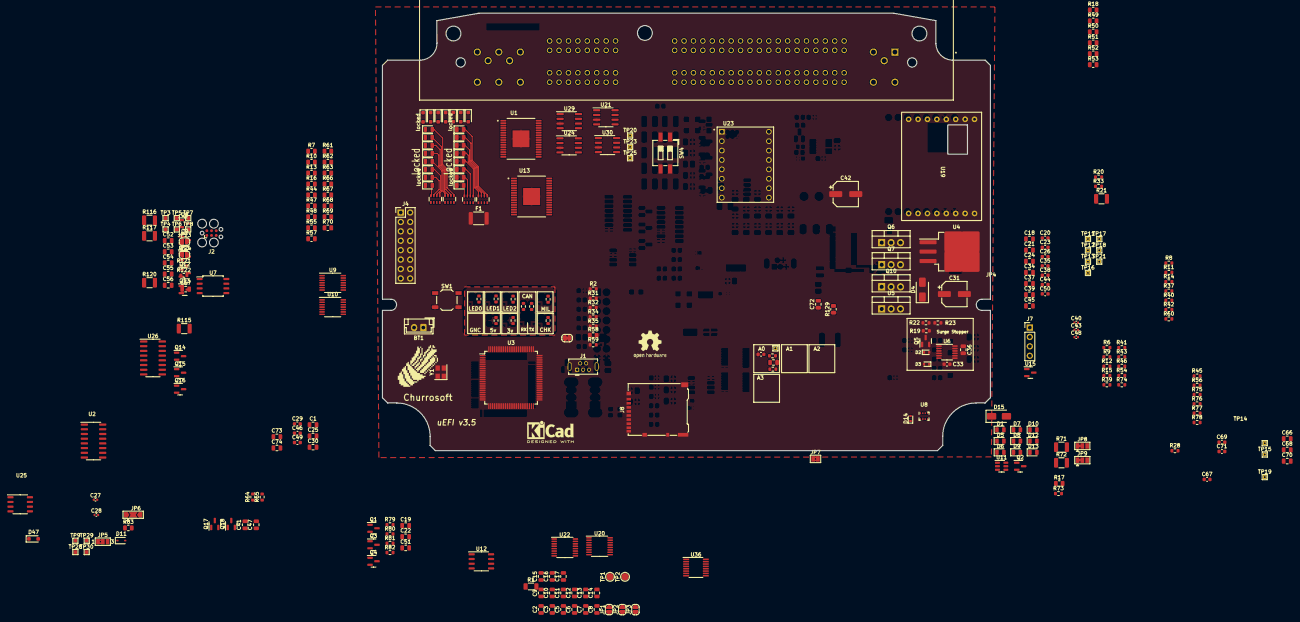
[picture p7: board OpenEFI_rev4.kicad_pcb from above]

Board: 4 copper layers, 164.0 x 118.0 mm, 293 parts (0 on the bottom side), 205 nets.

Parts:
BT1: Battery_Cell; JST_EH_B2B-EH-A_1x02_P2.50mm_Vertical
C1, C5, C9, C10, C11, C12, C13, C14, C15, C17, C18, C21, C24, C25, C30, C32, C34, C36, C37, C39, C45, C66, C68, C70: 100nF; C_0805_2012Metric
C2, C3: 15pF; C_0805_2012Metric
C4, C20, C23, C26, C29, C35, C38, C44, C46, C49, C50, C67, C69, C71: 0.22uF; C_0603_1608Metric
C6, C73: 1uF; C_0805_2012Metric
C7, C8: 2.2uF; C_0805_2012Metric
C16: 4.7uF; C_0805_2012Metric
C19, C22, C41, C51, C52, C53, C54, C55, C56, C57, C72: 0.01uF; C_0805_2012Metric
C27, C28: 47p; C_0402_1005Metric
C31, C42: 100uF ±20% 35V; CP_Elec_6.3x7.7
C33: 47nF; C_0603_1608Metric
C40, C43: 1u; C_0402_1005Metric
C47: 4700pF; C_0805_2012Metric
C48: 100n; C_0402_1005Metric
C74: 0.1uF; C_0805_2012Metric
Churrosoft: SYM_Hot_Large; churro_new_v4
D1, D5, D6, D7, D8, D9, D10, D12, D13, D16, D17, D18, D19, D20, D21, D22, D43, D63, D65, D67, D69, D71, D73, D75, D77: LED; LED_0805_2012Metric
D2, D3: 1N4148; D_SOD-523
D4: SMAJ58CA; D_SMA
D11: MM3Z24VT1G; D_SOD-323
D14: 1N914WT; D_SOD-523
D15: SS26; D_SMA
D47, D64, D66, D68, D70, D72, D74, D76: D; D_SOD-323_HandSoldering
F1: Polyfuse; Fuse_1812_4532Metric
J1: USB_B; USB_Mini-B_Tensility_54-00023_Vertical
J2: Tag connect; Tag-Connect_TC2030-IDC-FP_2x03_P1.27mm_Vertical
J4: Conn_02x08_Odd_Even; PinHeader_2x08_P2.54mm_Vertical
J6: 1241434-1; TE_1241434-1
J7: Conn_01x04; PinHeader_1x04_P2.54mm_Vertical
J8: Micro_SD_Card_Det1; microSD_HC_Hirose_DM3AT-SF-PEJM5
JP1, JP2, JP3, JP23, JP24: SolderJumper_2_Open; SolderJumper-2_P1.3mm_Open_RoundedPad1.0x1.5mm
JP4: Jumper_NO_Small; SolderJumper-2_P1.3mm_Open_RoundedPad1.0x1.5mm
JP5: SolderJumper-3_P1.3mm_Bridged2Bar12_Pad1.0x1.5mm_NumberLabe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
JP6: SolderJumper_3_Bridged12; SolderJumper-3_P2.0mm_Open_TrianglePad1.0x1.5mm
JP7: Jumper_2_Open; SolderJumper-2_P1.3mm_Bridged2Bar_Pad1.0x1.5mm
JP8, JP9: Jumper_3_Bridged12; SolderJumper-3_P1.3mm_Bridged12_Pad1.0x1.5mm
LOGO1: Logo_Open_Hardware_Large; OSHW-Logo2_9.8x8mm_SilkScreen
Q1, Q2, Q3, Q4, Q12, Q13, Q14, Q15, Q16, Q17, Q18: AO3400A; SOT-23
Q5, Q8, Q9, Q11: SS8050; SOT-23
Q6, Q7: IRLZ44N; TO-220-3_Vertical
Q10: IRF540N; TO-220-3_Vertical
R1: 120R; R_1206_3216Metric
R2, R59, R121, R122: 10k; R_0603_1608Metric
R3, R4, R5, R24, R25, R26, R27, R29, R30: 4.7k; R_0603_1608Metric
R6, R9, R12, R15, R36, R39, R41, R43, R46, R54, R74: 2.49k +-1%; R_0603_1608Metric
R7, R44, R48, R61, R63, R66, R69, R70: 348k; R_0805_2012Metric
R8, R11, R14, R37, R38, R40, R42, R45, R56, R60, R75, R76, R77, R78: 470R; R_0603_1608Metric
R10, R13, R47, R55, R57, R62, R67, R68: 180k; R_0805_2012Metric
R16: 604R; R_0805_2012Metric
R17, R18, R49, R50, R51, R52, R53, R58, R83, R129: 10k; R_0805_2012Metric
R19: 1M 1/10W; R_0603_1608Metric
R20, R33, R73: 10R 1/10W; R_0603_1608Metric
R21: 0.01R; R_1210_3225Metric
R22: 57.6K 1/10W; R_0603_1608Metric
R23: 4.99K 1/10W; R_0603_1608Metric
R28: 3.88k; R_0603_1608Metric
R31, R32, R34, R64, R65, R79, R80, R81, R82: 1k; R_0603_1608Metric
R35: 100k; R_0603_1608Metric
R71, R72, R116, R117: 10K 1/2W; R_1210_3225Metric
R115, R120: 4.99K 1/2W; R_1210_3225Metric
RN1, RN2, RN3, RN4: 1k; R_Array_Convex_4x0603
SW1: SW_Push; SW_SPST_TL3342
SW4: SW_DIP_x02; SW_DIP_SPSTx02_Slide_6.7x6.64mm_W8.61mm_P2.54mm_LowProfile
SYM1: SYM_Hot_Small; KiCad-Logo2_5mm_SilkScreen
TP1: BOOT0; TestPoint_Pad_D2.0mm
TP2: BOOT1; TestPoint_Pad_D2.0mm
TP3, TP4, TP5, TP6, TP7, TP8, TP9, TP28, TP29, TP30: TestPoint; TestPoint_Pad_1.0x1.0mm
TP10, TP11, TP12, TP13, TP14, TP15, TP16, TP17, TP18, TP19, TP20, TP21, TP23, TP25: TestPoint_Alt; TestPoint_THTPad_1.0x1.0mm_Drill0.5mm
U1, U13: MCZ33810EK; SOP65P1030X245-33N
U2: 74HC4851; SOIC-16_3.9x9.9mm_P1.27mm
U3: STM32F407VGTx; LQFP-100_14x14mm_P0.5mm
U4: MIC2940A-3.3WU; TO-263-3_TabPin2
U5: MIC2940A-5.0WT; TO-220-3_Vertical
U6: LT4363IMS; MSOP-12_3x4mm_P0.65mm
U7: 25LCxxx; SOIC-8_5.275x5.275mm_P1.27mm
U8: BMP280; Bosch_LGA-8_2x2.5mm_P0.65mm_ClockwisePinNumbering
U9, U10: LMV324; TSSOP-14_4.4x5mm_P0.65mm
U11: SRV05-4; SOT-23-6
U12, U25: TJA1051T-3; SOP-8_3.9x4.9mm_P1.27mm
U15: REF3033; SOT-23
U19: f042_wideband_module; rusEFI_WBO
U20, U22: TPL7407LAPWR; TSSOP-16_4.4x5mm_P0.65mm
U21, U24, U29, U30: TC4424A; SOIC-8_3.9x4.9mm_P1.27mm
U23: PaP_Driver_v1; MODULE_A4988_STEPPER_MOTOR_DRIVER_CARRIER
U26: SP720ABTG; SOP-16_3.9x9.9mm_P1.27mm
U36: MAX9926UAEE+; QSOP-16_3.9x4.9mm_P0.635mm
Y1: 25MHz; Crystal_SMD_3225-4Pin_3.2x2.5mm

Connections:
5V_ENABLE: R33.1, U3.16 (PC1)
+3V3: C5.1, C6.1, C10.1, C11.1, C12.1, C13.1, C14.1, C15.1, C16.1, C17.1, C31.1, D1.2 (A), D5.2 (A), D7.2 (A), D8.2 (A), D9.2 (A), D10.2 (A), D12.2 (A), D13.2 (A), D14.2 (A), J2.1, J4.1, JP1.1 (A), JP2.1 (A), JP3.1 (A), JP5.2 (C), Q1.1 (G), Q2.1 (G), Q3.1 (G), Q4.1 (G), Q14.1 (G), Q15.1 (G), Q16.1 (G), Q17.1 (G), Q18.1 (G), R49.2, R51.2, R53.2, R59.1, R64.1, R65.1, R79.2, R80.2, R81.2, R82.2, R121.1, R122.1, U1.8 (VDD), U3.11 (VDD), U3.19 (VDD), U3.21 (VREF+), U3.28 (VDD), U3.50 (VDD), U3.75 (VDD), U3.100 (VDD), U4.3 (OUT), U7.3 (~WP), U7.7 (~HOLD), U7.8 (VCC), U8.6 (VDDIO), U8.8 (VDD), U9.4 (V+), U10.4 (V+), U12.5 (VIO), U13.8 (VDD), U23.5 (RESET), U23.6 (SLEEP), U26.16 (V+)
+5C: C40.1, D6.2 (A), D15.1 (K), F1.1, J4.2, Q10.3 (S), R6.2, R9.2, R12.2, R15.2, R18.1, R36.2, R39.2, R41.2, R43.2, R46.2, R50.1, R52.1, R54.2, R74.2, U2.16 (Vdd), U5.3 (OUT), U12.3 (VCC), U15.1 (IN), U19.1 (5V), U25.3 (VCC), U36.14 (VCC)
+12V: C42.1, JP4.2, JP6.3 (B), R21.1, R22.1, R28.2, R35.1, RN1.5 (R4.2), RN1.6 (R3.2), RN1.7 (R2.2), RN1.8 (R1.2), RN2.5 (R4.2), RN2.6 (R3.2), RN2.7 (R2.2), RN2.8 (R1.2), U1.25 (VPWR), U4.1 (IN), U5.1 (IN), U6.2 (OUT), U13.25 (VPWR), U20.9 (COM), U22.9 (COM), U23.16 (VMOT)
+12VA: D2.2 (A), JP4.1, Q5.2 (E), Q6.3 (S)
/ACC_DET: R58.1, U3.80 (PC12)
/AUX_CS_1: J4.3, U3.45 (PE14)
/AUX_CS_2: J4.5, U3.46 (PE15)
/AUX_IN_1: J4.7, U3.91 (PB5)
/AUX_IN_2: J4.9, U3.92 (PB6)
/AUX_IN_3: J4.11, U3.93 (PB7)
/AUX_IN_4: J4.13, U3.95 (PB8)
/AUX_OUT_1: J4.10, U3.33 (PC4)
/AUX_OUT_2: J4.12, U3.34 (PC5)
/AUX_OUT_3: J4.14, U3.35 (PB0)
/CHK: Q9.3 (C), R30.2
/CHK_OUT: R32.1, U3.66 (PC9), U20.6 (IN6)
/CKP: C41.1, C47.1, Q18.2 (S), R65.2, R122.2, TP7.1, U3.63 (PC6), U36.5 (COUT2)
/CKP/CMP_sensors/CKP_VR: C55.1, JP9.1 (A), R117.1
/CKP/CMP_sensors/IN1+: C54.1, R72.2, R115.1, TP4.1, U36.16 (IN1+)
/CKP/CMP_sensors/IN1-: C54.2, JP23.1 (A), R71.2, TP5.1, U36.15 (IN1-)
/CKP/CMP_sensors/IN2+: C57.2, JP24.1 (A), R117.2, TP6.1, U36.10 (IN2-)
/CKP/CMP_sensors/IN2-: C57.1, R116.2, R120.1, TP3.1, U36.9 (IN2+)
/CMP: Q17.2 (S), R64.2, R121.2, TP8.1, U3.64 (PC7), U36.4 (COUT1)
/ECN1: U1.24 (GIN0), U3.57 (PD10)
/ECN2: U1.23 (GIN1), U3.58 (PD11)
/INY1: U1.10 (DIN0), U3.55 (PD8)
/INY2: U1.11 (DIN1), U3.56 (PD9)
/LED0: R25.2, U3.7 (PC13)
/LED1: R26.2, U3.8 (PC14)
/LED2: R27.2, U3.9 (PC15)
/LED_CAN_RX: R24.2, U3.87 (PD6)
/LED_CAN_TX: R5.2, U3.88 (PD7)
/MEMORY_CS: TP9.1, U3.44 (PE13), U7.1 (~CS)
/MIL: Q8.3 (C), R29.2
/MIL_OUT: R31.1, U3.65 (PC8), U20.7 (IN7)
/MTR_DIR: U3.39 (PE8), U23.8 (DIR)
/MTR_ENABLE: U3.41 (PE10), U23.1 (ENABLE)
/MTR_FAULT: JP5.3 (B), U3.40 (PE9)
/MTR_STEP: U3.38 (PE7), U23.7 (STEP)
/MUX_A: Q16.2 (S), R49.1, U3.83 (PD2)
/MUX_B: Q14.2 (S), R51.1, U3.84 (PD3)
/MUX_C: Q15.2 (S), R53.1, U3.85 (PD4)
/NRST: C9.2, J2.3, SW1.1, U3.14 (NRST)
/PMIC1_CS: U1.4 (~CS), U3.78 (PC10)
/PMIC1_ENABLE: R83.2, R129.2, U1.9 (~OUTEN), U3.51 (PB12)
/PMIC2_CS: U3.79 (PC11), U13.4 (~CS)
/PMIC2_ENABLE: U3.52 (PB13), U13.9 (~OUTEN)
/PMIC/FB0: U1.2 (FB0), U13.2 (FB0)
/PMIC/FB1: U1.15 (FB1), U13.15 (FB1)
/PMIC/FB2: U1.31 (FB2), U13.31 (FB2)
/PMIC/FB3: U1.18 (FB3), U13.18 (FB3)
/PMIC/GD0: U1.3 (GD0), U13.3 (GD0), U21.2 (IN_A), U29.2 (IN_A)
/PMIC/GD1: U1.14 (GD1), U13.14 (GD1), U21.4 (IN_B), U29.4 (IN_B)
/PMIC/GD2: U1.30 (GD2), U13.30 (GD2), U24.2 (IN_A), U30.2 (IN_A)
/PMIC/GD3: U1.19 (GD3), U13.19 (GD3), U24.4 (IN_B), U30.4 (IN_B)
/RPM_OUT: R34.1, U3.42 (PE11)
/R_AAC: U3.3 (PE4), U22.1 (IN1), U22.2 (IN2)
/R_ECN_INY: U3.1 (PE2), U22.5 (IN5), U22.6 (IN6)
/R_GNC_GLP: U3.2 (PE3), U22.3 (IN3), U22.4 (IN4)
/R_LMB: U3.97 (PE0), U22.7 (IN7)
/SPI2_MISO: J4.6, J7.3, TP30.1, U1.7 (SO), U3.53 (PB14), U7.2 (MISO), U13.7 (SO)
/SPI2_MOSI: J4.8, J7.2, TP29.1, U1.6 (SI), U3.54 (PB15), U7.5 (MOSI), U13.6 (SI)
/SPI2_SCK: J4.4, J7.1, TP28.1, U1.5 (SCLK), U3.47 (PB10), U7.6 (SCK), U13.5 (SCLK)
/SYS_SWCLK: J2.4, U3.76 (PA14)
/SYS_SWDIO: J2.2, U3.72 (PA13)
/SYS_SWO: J2.6, U3.89 (PB3)
/Sensores/A: Q16.3 (D), R18.2, U2.11 (A)
/Sensores/AUX_CH1: C4.1, R38.1, TP10.1, U26.1 (I1)
/Sensores/AUX_CH2: C20.1, R11.1, TP11.1, U26.2 (I2)
/Sensores/AUX_CH3: C23.1, R14.1, TP12.1, U26.3 (I3)
/Sensores/AUX_CH4: C26.1, R37.1, TP13.1, U26.4 (I4)
/Sensores/AUX_CH5: C35.1, R8.1, TP16.1, U26.5 (I5)
/Sensores/AUX_CH6: C38.1, R60.1, TP17.1, U26.6 (I6)
/Sensores/AUX_CH7: C44.1, R42.1, TP18.1, U26.7 (I7)
/Sensores/AUX_CH8: C50.1, R40.1, TP21.1, U26.9 (I8)
/Sensores/B: Q14.3 (D), R50.2, U2.10 (B)
/Sensores/C: Q15.3 (D), R52.2, U2.9 (C)
/Sensores/CAN_RX: U19.5 (CAN_RX), U25.4 (RXD)
/Sensores/CAN_TX: U19.6 (CAN_TX), U25.1 (TXD)
/Sensores/CH_CLT: C69.1, R45.1, TP15.1, U26.14 (I13)
/Sensores/CH_IAT: C67.1, R47.2, R75.1, TP14.1, U26.15 (I14)
/Sensores/CH_MAP: C46.1, R13.2, R77.1, TP23.1, U26.11 (I10)
/Sensores/CH_O2: C49.1, R55.2, R78.1, TP25.1, U26.10 (I9)
/Sensores/CH_TPS: C71.1, R10.2, R76.1, TP19.1, U26.12 (I11)
/Sensores/CH_VBATT: C29.1, R56.1, R62.2, R67.2, TP20.1, U26.13 (I12)
/Sensores/LSU_Heater-: U19.11 (HEATER-), U19.12 (HEATER-)
/Sensores/mux_out: R57.2, U2.3 (OUT)
/TIM9_CH1: U3.4 (PE5), U20.1 (IN1), U20.2 (IN2), U20.3 (IN3)
/TIM9_CH2: U3.5 (PE6), U20.4 (IN4), U20.5 (IN5)
/USB_D+: J1.3 (D+), U3.71 (PA12), U11.3 (IO2)
/USB_D-: J1.2 (D-), U3.70 (PA11), U11.1 (IO1)
/VBUS: D15.2 (A), J1.1 (VBUS), U3.68 (PA9), U11.5 (VP)
A1: D11.1 (K), Q12.3 (D)
B1: C18.1, C21.1, C24.1, C32.1, C34.1, C37.1, C39.1, C45.1, R6.1, R8.2, R9.1, R11.2, R12.1, R14.2, R15.1, R36.1, R37.2, R38.2, R39.1, R40.2, R41.1, R42.2, R43.1, R60.2
B4: U20.12 (OUT5), U20.13 (OUT4)
C4: U20.14 (OUT3), U20.15 (OUT2), U20.16 (OUT1)
CAN+: C27.2, R1.2, U12.7 (CANH), U25.7 (CANH)
CAN-: C28.1, JP7.1 (A), U12.6 (CANL), U25.6 (CANL)
CKP-: C56.1, R116.1
CMP-: C52.1, R71.1
D4: U22.11 (OUT6), U22.12 (OUT5)
E1: C30.1, C66.1, C68.1, C70.1, R45.2, R46.1, R54.1, R74.1, R75.2, R76.2, R77.2
G3: U22.13 (OUT4), U22.14 (OUT3)
GND: BT1.2 (-), C1.2, C2.2, C3.2, C4.2, C5.2, C6.2, C7.2, C8.2, C9.1, C10.2, C11.2, C12.2, C13.2, C14.2, C15.2, C16.2, C17.2, C18.2, C19.1, C20.2, C21.2, C22.1, C23.2, C24.2, C25.2, C26.2, C27.1, C28.2, C29.2, C30.2, C31.2, C32.2, C33.2, C34.2, C35.2, C36.2, C37.2, C38.2, C39.2, C40.2, C42.2, C43.2, C44.2, C45.2, C46.2, C48.2, C49.2, C50.2, C51.1, C52.2, C53.2, C55.2, C56.2, C66.2, C67.2, C68.2, C69.2, C70.2, C71.2, C72.1, C73.1, C74.2, D3.2 (A), D4.2 (A2), D11.2 (A), D16.1 (K), D17.1 (K), D18.1 (K), D19.1 (K), D20.1 (K), D21.1 (K), D22.1 (K), D77.1 (K), J1.4 (GND), J1.5 (Shield), J2.5, J4.15, J4.16, J7.4, Q8.2 (E), Q9.2 (E), Q11.2 (E), Q12.2 (S), Q13.2 (S), R2.2, R3.2, R4.2, R7.2, R16.1, R23.1, R44.2, R48.2, R61.2, R63.2, R66.2, R69.2, R70.2, R83.1, R129.1, SW1.2, SW4.1, SW4.2, U1.33 (GND), U2.6 (EN), U2.8 (GND), U3.10 (VSS), U3.20 (VSSA), U3.27 (VSS), U3.74 (VSS), U3.99 (VSS), U4.2 (GND), U5.2 (GND), U6.9 (GND), U7.4 (GND), U8.1 (GND), U8.7 (GND), U9.11 (V-), U10.11 (V-), U11.2 (VN), U12.2 (GND), U12.8 (S), U13.33 (GND), U15.3 (GND), U19.2 (GND), U19.9 (HEAT_GND), U19.10 (HEAT_GND2), U20.8 (GND), U21.3 (GND), U22.8 (GND), U23.9 (GND), U23.15 (GND), U24.3 (GND), U25.2 (GND), U25.8 (S), U26.8 (GND), U29.3 (GND), U30.3 (GND), U36.1 (INT_THRS1), U36.3 (BIAS1), U36.6 (BIAS2), U36.8 (INT_THRS2), U36.11 (GND), U36.13 (ZERO_EN), Y1.2, Y1.4
H1: Q13.3 (D), R59.2
H3: U22.15 (OUT2), U22.16 (OUT1)
IGN1: RN3.8 (R1.2), U21.7 (OUT_A), U29.7 (OUT_A)
IGN2: RN3.7 (R2.2), U21.5 (OUT_B), U29.5 (OUT_B)
IGN3: RN3.5 (R4.2), U24.7 (OUT_A), U30.7 (OUT_A)
IGN4: RN3.6 (R3.2), U24.5 (OUT_B), U30.5 (OUT_B)
IGN_V+: C73.2, C74.1, JP6.2 (C), U21.6 (VDD), U24.6 (VDD), U29.6 (VDD), U30.6 (VDD)
INJ1: D47.1 (K), U1.1 (OUT0), U13.1 (OUT0)
INJ2: D64.1 (K), U1.16 (OUT1), U13.16 (OUT1)
INJ3: D66.1 (K), U1.32 (OUT2), U13.32 (OUT2)
INJ4: D68.1 (K), U1.17 (OUT3), U13.17 (OUT3)
K1: C1.1, R78.2
MCU-D23: C19.2, C22.2, C51.2, C72.2, Q1.3 (D), Q2.3 (D), Q3.3 (D), Q4.3 (D), R79.1, R80.1, R81.1, R82.1
unnamed: BT1.1 (+), D14.1 (K), U3.6 (VBAT)
unnamed: C25.1, R16.2, R28.1, R56.2
unnamed: C41.2, SW4.4
unnamed: C47.2, SW4.3
unnamed: D1.1 (K), R5.1
unnamed: D2.1 (K), Q5.1 (B), R17.2
unnamed: D3.1 (K), R17.1
unnamed: D4.1 (A1), Q6.2 (D), Q7.2 (D), U6.5 (VCC)
unnamed: D5.1 (K), R24.1
unnamed: D6.1 (K), R4.1
unnamed: D7.1 (K), R3.1
unnamed: D8.1 (K), R25.1
unnamed: D9.1 (K), R26.1
unnamed: D10.1 (K), R27.1
unnamed: D12.1 (K), R29.1
unnamed: D13.1 (K), R30.1
unnamed: D16.2 (A), RN3.2 (R2.1)
unnamed: D17.2 (A), RN3.3 (R3.1)
unnamed: D18.2 (A), RN3.4 (R4.1)
unnamed: D19.2 (A), RN4.1 (R1.1)
unnamed: D20.2 (A), RN4.2 (R2.1)
unnamed: D21.2 (A), RN4.3 (R3.1)
unnamed: D22.2 (A), RN4.4 (R4.1)
unnamed: D43.2 (A), RN1.1 (R1.1)
unnamed: D43.1 (K), D47.2 (A)
unnamed: D63.2 (A), RN1.2 (R2.1)
unnamed: D63.1 (K), D64.2 (A)
unnamed: D65.2 (A), RN1.3 (R3.1)
unnamed: D65.1 (K), D66.2 (A)
unnamed: D67.2 (A), RN1.4 (R4.1)
unnamed: D67.1 (K), D68.2 (A)
unnamed: D69.2 (A), RN2.1 (R1.1)
unnamed: D69.1 (K), D70.2 (A)
unnamed: D71.2 (A), RN2.2 (R2.1)
unnamed: D71.1 (K), D72.2 (A)
unnamed: D73.2 (A), RN2.3 (R3.1)
unnamed: D73.1 (K), D74.2 (A)
unnamed: D75.2 (A), RN2.4 (R4.1)
unnamed: D75.1 (K), D76.2 (A)
unnamed: D77.2 (A), RN3.1 (R1.1)
unnamed: JP1.2 (B), U23.3 (M1)
unnamed: JP2.2 (B), U23.2 (M0)
unnamed: JP3.2 (B), U23.4 (M2)
unnamed: JP5.1 (A), U23.10 (FAULT)
unnamed: F1.2, JP6.1 (A)
unnamed: JP7.2 (B), R1.1
unnamed: C53.1, JP8.1 (A), R72.1
unnamed: JP8.3 (B), Q17.3 (D)
unnamed: JP9.3 (B), Q18.3 (D)
unnamed: JP23.2 (B), R115.2
unnamed: JP24.2 (B), R120.2
unnamed: Q5.3 (C), R19.2, R73.2
unnamed: Q6.1 (G), R73.1
unnamed: Q7.1 (G), R20.1
unnamed: Q7.3 (S), R21.2, U6.3 (SNS)
unnamed: Q8.1 (B), R31.2
unnamed: Q9.1 (B), R32.2
unnamed: Q10.1 (G), R33.2
unnamed: Q11.1 (B), R34.2
unnamed: Q11.3 (C), Q12.1 (G), R35.2
unnamed: Q13.1 (G), R58.2
unnamed: R2.1, TP1.1, U3.94 (BOOT0)
unnamed: TP2.1, U3.37 (PB2)
unnamed: C7.1, U3.49 (VCAP_1)
unnamed: C8.1, U3.73 (VCAP_2)
unnamed: R22.2, R23.2, U6.1 (FB)
unnamed: C33.1, R19.1, R20.2, U6.4 (GATE)
unnamed: C36.1, U6.12 (TMR)
unnamed: R47.1, R48.1, U9.3 (+)
unnamed: U9.1, U9.2 (-)
unnamed: R7.1, R10.1, U9.5 (+)
unnamed: U9.6 (-), U9.7
unnamed: R13.1, R44.1, U9.10 (+)
unnamed: U9.8, U9.9 (-)
unnamed: R62.1, R63.1, U9.12 (+)
unnamed: U9.13 (-), U9.14
unnamed: R55.1, R61.1, U10.3 (+)
unnamed: U10.1, U10.2 (-)
unnamed: R67.1, R69.1, U10.5 (+)
unnamed: U10.6 (-), U10.7
unnamed: R68.1, R70.1, U10.10 (+)
unnamed: U10.8, U10.9 (-)
unnamed: R57.1, R66.1, U10.12 (+)
unnamed: U10.13 (-), U10.14
OSC_IN: C2.1, U3.12 (PH0), Y1.1
OSC_OUT: C3.1, U3.13 (PH1), Y1.3
VDDA: C43.1, C48.1, U3.22 (VDDA), U15.2 (OUT)

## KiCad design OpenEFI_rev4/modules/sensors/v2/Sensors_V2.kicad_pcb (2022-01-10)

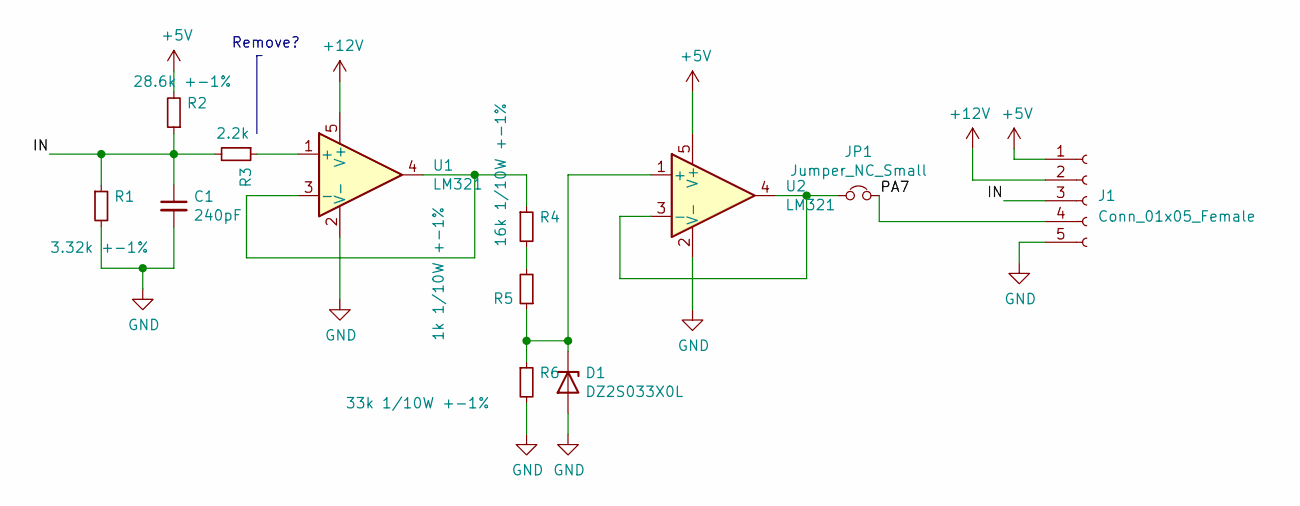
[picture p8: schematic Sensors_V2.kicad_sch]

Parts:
C1: 240pF; C_0603_1608Metric; LCSC C185593
D1: DZ2S033X0L; D_MiniMELF; LCSC C8056
J1: Conn_01x05_Female; PinHeader_1x05_P1.27mm_Horizontal
JP1: Jumper_NC_Small; SolderJumper-2_P1.3mm_Open_TrianglePad1.0x1.5mm
R1: 3.32k +-1%; R_0603_1608Metric; LCSC C234508
R2: 28.6k +-1%; R_0603_1608Metric; LCSC C217931
R3: 2.2k; R_0603_1608Metric; LCSC C309092
R4: 16k 1/10W +-1%; R_0603_1608Metric; LCSC C217760
R5: 1k 1/10W +-1%; R_0603_1608Metric; LCSC C217840
R6: 33k 1/10W +-1%; R_0603_1608Metric
U1, U2: LM321; SOT-23-5

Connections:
+5V: J1.1, R2.2, U2.5 (V+)
+12V: J1.2, U1.5 (V+)
/IN: C1.1, J1.3, R1.1, R2.1, R3.2
GND: C1.2, D1.2 (A), J1.5, R1.2, R6.2, U1.2 (V-), U2.2 (V-)
unnamed: D1.1 (K), R5.1, R6.1, U2.1 (+)
unnamed: J1.4, JP1.2
unnamed: JP1.1, U2.3 (-), U2.4
unnamed: R3.1, U1.1 (+)
unnamed: R4.1, U1.3 (-), U1.4
unnamed: R4.2, R5.2

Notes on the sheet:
Remove?

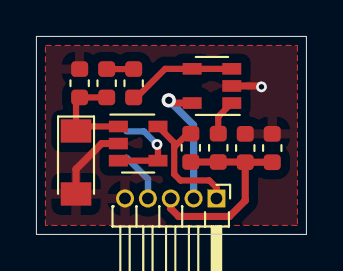
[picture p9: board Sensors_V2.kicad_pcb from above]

Board: 2 copper layers, 15.0 x 11.0 mm, 12 parts (1 on the bottom side), 10 nets.

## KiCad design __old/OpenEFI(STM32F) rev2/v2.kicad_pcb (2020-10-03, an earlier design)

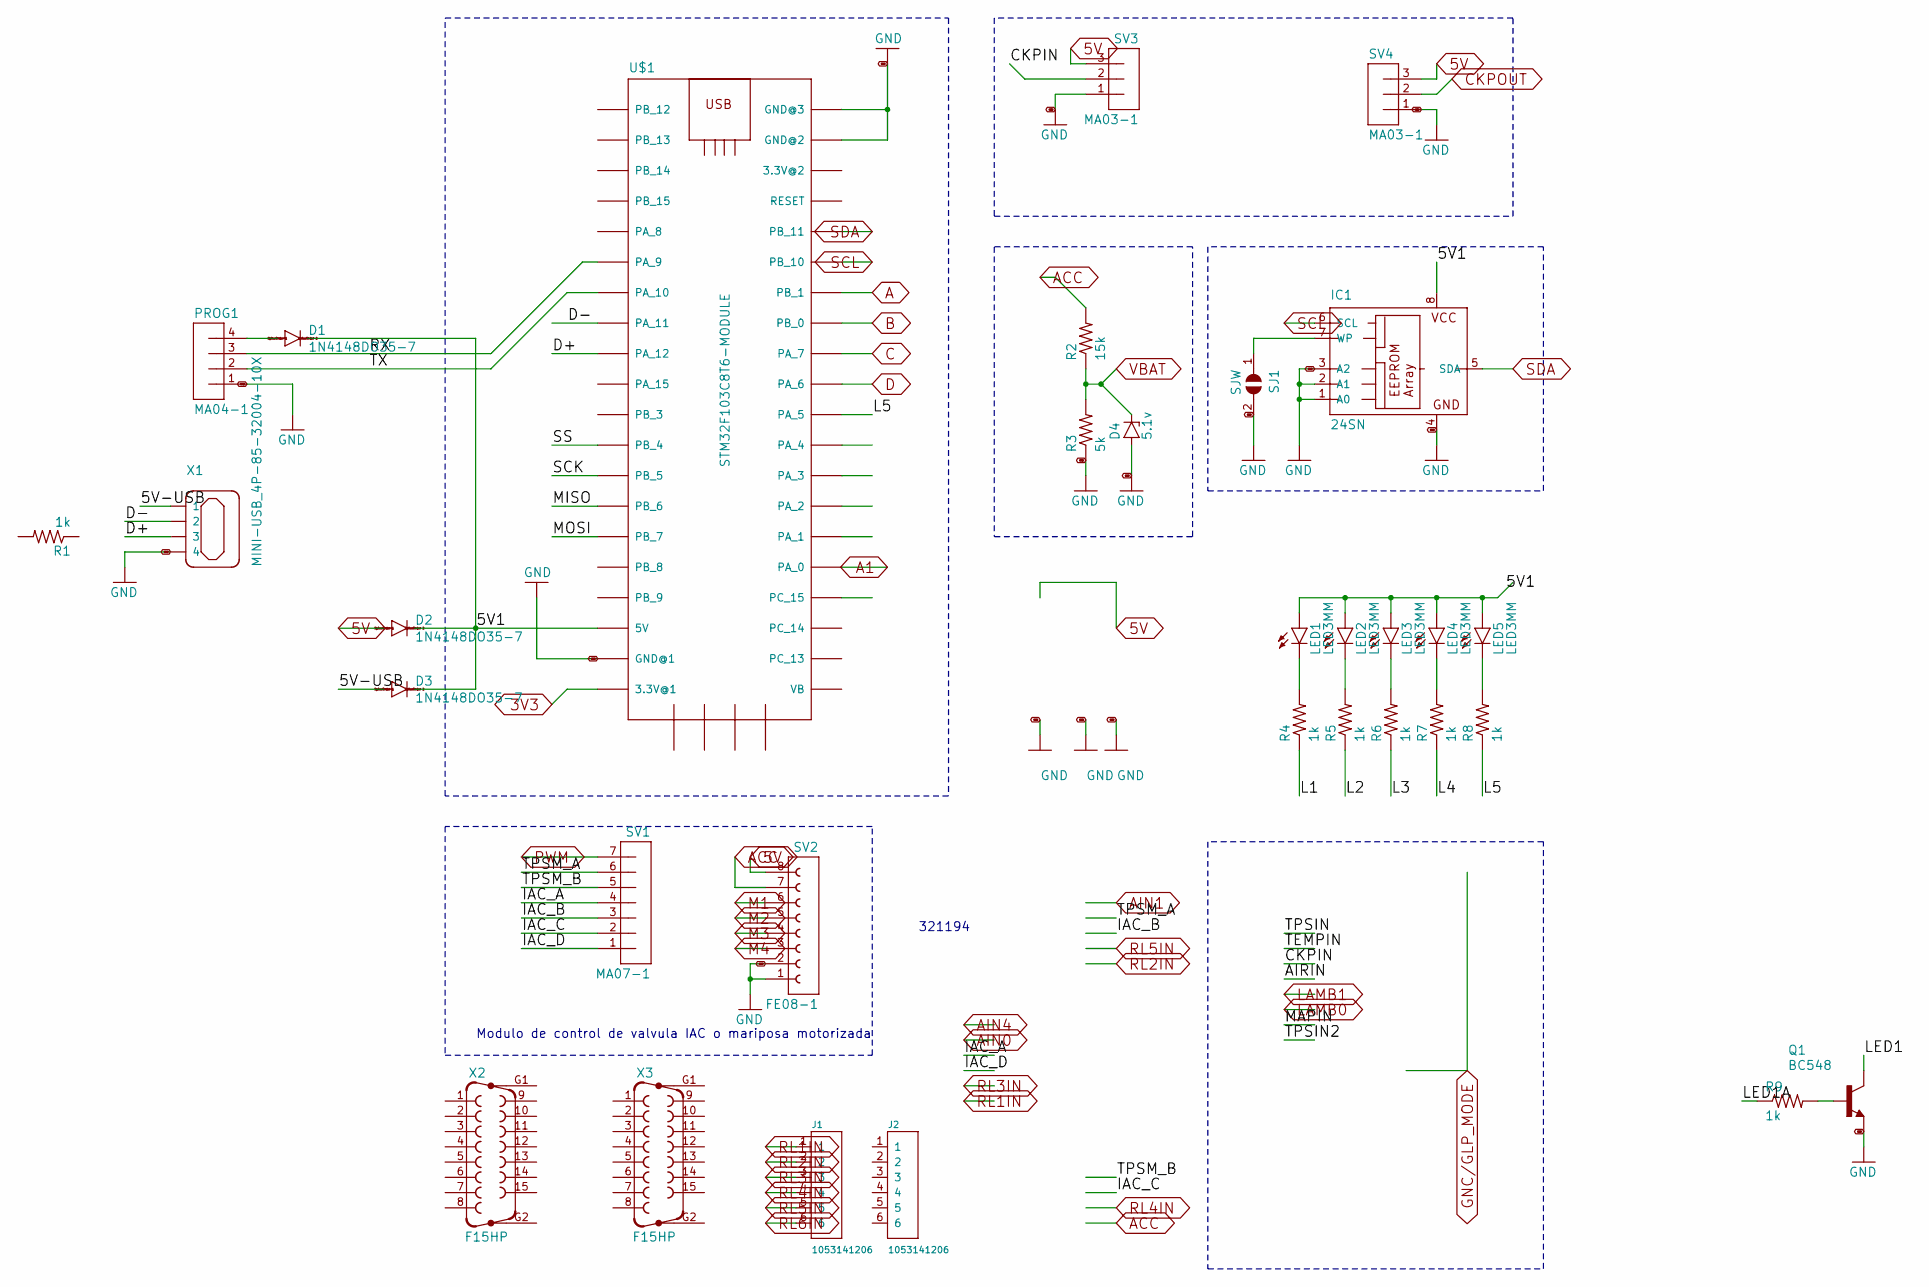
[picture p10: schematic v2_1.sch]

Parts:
D1, D2, D3: 1N4148DO35-7; DO35-7
D4: 5.1v; ZDIO-5
IC1: 24SN; SO-08
J1, J2: 1053141206; MOLEX_1053141206
LED1, LED2, LED3, LED4, LED5: LED3MM
PROG1: MA04-1
Q1: BC548; TO92-EBC
R1, R4, R5, R6, R7, R8, R9: 1k; 0204_5
R2: 15k; 0204_5
R3: 5k; 0204_5
SJ1: SJW
SV1: MA07-1
SV2: FE08-1; FE08
SV3, SV4: MA03-1
U$1: STM32F103C8T6-MODULE
X1: MINI-USB_4P-85-32004-10X; 85-32004-10X
X2, X3: F15HP

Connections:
3V3: U$1.3.3V_1 (3.3V@1); also elsewhere on the board
5V: D2.A, SV2.8, SV3.3, SV4.3; also elsewhere on the board
/v2_1/5V1: D1.C, D2.C, D3.C, IC1.8 (VCC), LED1.A, LED2.A, LED3.A, LED4.A, LED5.A, U$1.5V
/v2_1/5V-USB: D3.A, X1.1
/v2_1/CKPIN: SV3.2
/v2_1/D+: U$1.PA_12, X1.3
/v2_1/D-: U$1.PA_11, X1.2
/v2_1/IAC_A: SV1.4
/v2_1/IAC_B: SV1.3
/v2_1/IAC_C: SV1.2
/v2_1/IAC_D: SV1.1
/v2_1/L1: R4.1
/v2_1/L2: R5.1
/v2_1/L3: R6.1
/v2_1/L4: R7.1
/v2_1/L5: R8.1, U$1.PA_5
/v2_1/LED1: Q1.C
/v2_1/LED1A: R9.1
/v2_1/MISO: U$1.PB_6
/v2_1/MOSI: U$1.PB_7
/v2_1/RX: PROG1.3, U$1.PA_9
/v2_1/SCK: U$1.PB_5
/v2_1/SS: U$1.PB_4
/v2_1/TPSM_A: SV1.6
/v2_1/TPSM_B: SV1.5
/v2_1/TX: PROG1.2, U$1.PA_10
A: U$1.PB_1; also elsewhere on the board
A1: U$1.PA_0; also elsewhere on the board
ACC: R2.2, SV2.7; also elsewhere on the board
B: U$1.PB_0; also elsewhere on the board
C: U$1.PA_7; also elsewhere on the board
CKPOUT: SV4.2
D: U$1.PA_6; also elsewhere on the board
GND: D4.A, IC1.1 (A0), IC1.2 (A1), IC1.3 (A2), IC1.4 (GND), PROG1.1, Q1.E, R3.1, SJ1.2, SV2.1, SV2.2, SV3.1, SV4.1, U$1.GND_1 (GND@1), U$1.GND_2 (GND@2), U$1.GND_3 (GND@3), X1.4; also elsewhere on the board
M1: SV2.6; also elsewhere on the board
M2: SV2.5; also elsewhere on the board
M3: SV2.4; also elsewhere on the board
M4: SV2.3; also elsewhere on the board
unnamed: D1.A, PROG1.4
unnamed: IC1.7 (WP), SJ1.1
unnamed: LED1.K (C), R4.2
unnamed: LED2.K (C), R5.2
unnamed: LED3.K (C), R6.2
unnamed: LED4.K (C), R7.2
unnamed: LED5.K (C), R8.2
unnamed: Q1.B, R9.2
PWM: SV1.7
RL1IN: J1.1; also elsewhere on the board
RL2IN: J1.2; also elsewhere on the board
RL3IN: J1.3; also elsewhere on the board
RL4IN: J1.4; also elsewhere on the board
RL5IN: J1.5; also elsewhere on the board
RL6IN: J1.6; also elsewhere on the board
SCL: IC1.6 (SCL), U$1.PB_10; also elsewhere on the board
SDA: IC1.5 (SDA), U$1.PB_11; also elsewhere on the board
VBAT: D4.C, R2.1, R3.2; also elsewhere on the board

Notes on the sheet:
Modulo de control de valvula IAC o mariposa motorizada
321194

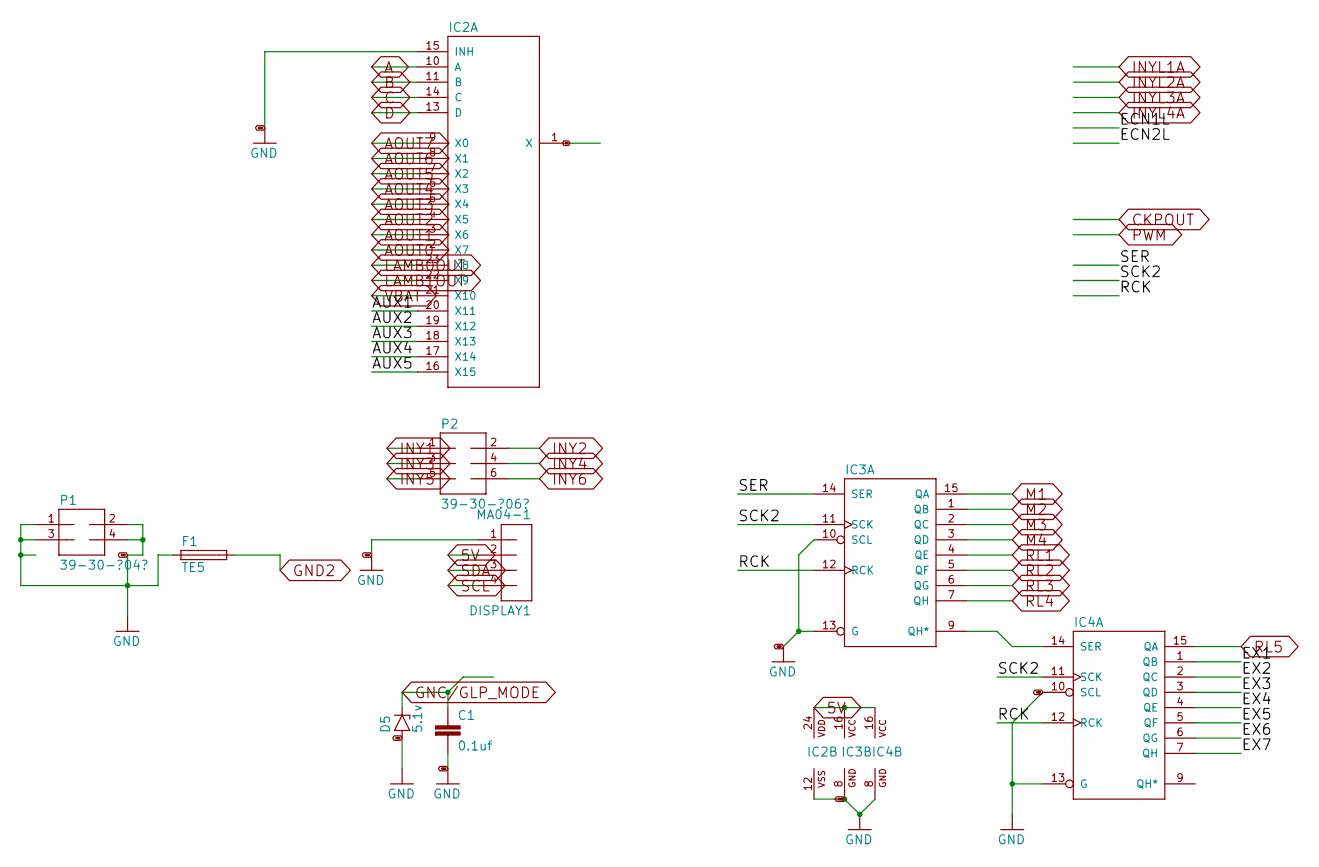
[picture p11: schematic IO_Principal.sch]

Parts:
C1: 0.1uf; C025-025X050
D5: 5.1v; ZDIO-5
DISPLAY1: MA04-1
F1: TE5
IC2: 4067D; SO24W
IC3, IC4: 74595D; SO16
P1: 39-30-?04?
P2: 39-30-?06?

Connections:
5V: DISPLAY1.2, IC2.24 (VDD), IC3.16 (VCC), IC4.16 (VCC); also elsewhere on the board
/IO Principal/AUX1: IC2.20 (X11)
/IO Principal/AUX2: IC2.19 (X12)
/IO Principal/AUX3: IC2.18 (X13)
/IO Principal/AUX4: IC2.17 (X14)
/IO Principal/AUX5: IC2.16 (X15)
/IO Principal/EX1: IC4.1 (QB)
/IO Principal/EX2: IC4.2 (QC)
/IO Principal/EX3: IC4.3 (QD)
/IO Principal/EX4: IC4.4 (QE)
/IO Principal/EX5: IC4.5 (QF)
/IO Principal/EX6: IC4.6 (QG)
/IO Principal/EX7: IC4.7 (QH)
/IO Principal/RCK: IC3.12 (RCK), IC4.12 (RCK)
/IO Principal/SCK2: IC3.11 (SCK), IC4.11 (SCK)
/IO Principal/SER: IC3.14 (SER)
A: IC2.10 (A); also elsewhere on the board
A0: IC2.1 (X); also elsewhere on the board
AOUT0: IC2.2 (X7); also elsewhere on the board
AOUT1: IC2.3 (X6); also elsewhere on the board
AOUT2: IC2.4 (X5); also elsewhere on the board
AOUT3: IC2.5 (X4); also elsewhere on the board
AOUT4: IC2.6 (X3); also elsewhere on the board
AOUT5: IC2.7 (X2); also elsewhere on the board
AOUT6: IC2.8 (X1); also elsewhere on the board
AOUT7: IC2.9 (X0); also elsewhere on the board
B: IC2.11 (B); also elsewhere on the board
C: IC2.14 (C); also elsewhere on the board
D: IC2.13 (D); also elsewhere on the board
GNC/GLP_MODE: C1.1, D5.C
GND: C1.2, D5.A, DISPLAY1.1, F1.1, IC2.12 (VSS), IC2.15 (INH), IC3.8 (GND), IC3.10 (SCL), IC3.13 (G), IC4.8 (GND), IC4.10 (SCL), IC4.13 (G), P1.1, P1.2, P1.3, P1.4; also elsewhere on the board
GND2: F1.2; also elsewhere on the board
INY1: P2.1; also elsewhere on the board
INY2: P2.2; also elsewhere on the board
INY3: P2.3; also elsewhere on the board
INY4: P2.4; also elsewhere on the board
INY5: P2.5; also elsewhere on the board
INY6: P2.6; also elsewhere on the board
LAMB0OUT: IC2.23 (X8); also elsewhere on the board
LAMB1OUT: IC2.22 (X9); also elsewhere on the board
M1: IC3.15 (QA); also elsewhere on the board
M2: IC3.1 (QB); also elsewhere on the board
M3: IC3.2 (QC); also elsewhere on the board
M4: IC3.3 (QD); also elsewhere on the board
unnamed: IC3.9 (QH*), IC4.14 (SER)
RL1: IC3.4 (QE); also elsewhere on the board
RL2: IC3.5 (QF); also elsewhere on the board
RL3: IC3.6 (QG); also elsewhere on the board
RL4: IC3.7 (QH); also elsewhere on the board
RL5: IC4.15 (QA); also elsewhere on the board
SCL: DISPLAY1.4; also elsewhere on the board
SDA: DISPLAY1.3; also elsewhere on the board
VBAT: IC2.21 (X10); also elsewhere on the board

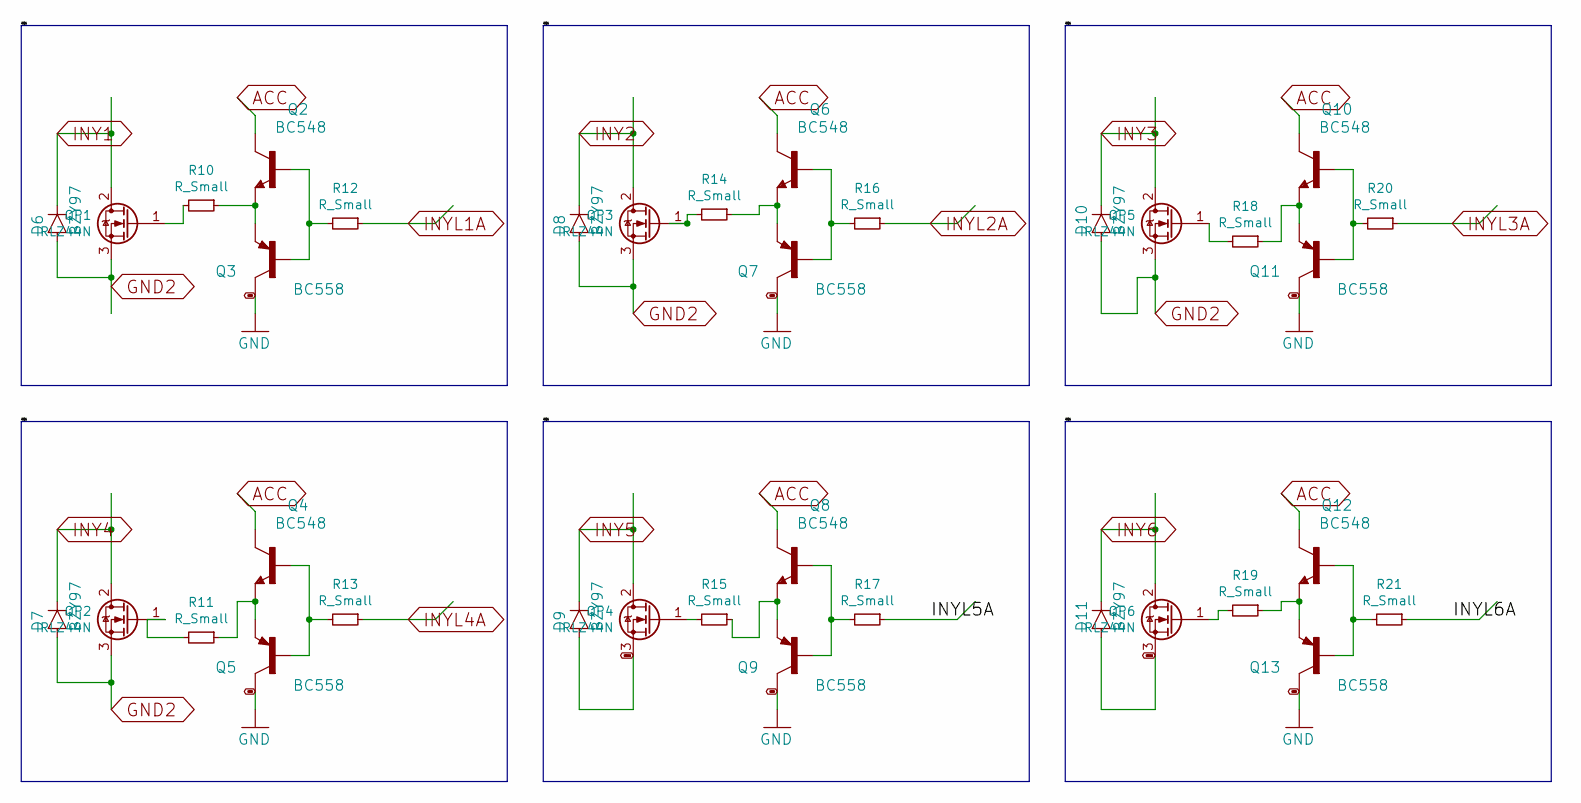
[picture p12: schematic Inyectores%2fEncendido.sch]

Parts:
D6, D7, D8, D9, D10, D11: BZY97; F126Z12
Q2, Q4, Q6, Q8, Q10, Q12: BC548; TO92-EBC
Q3, Q5, Q7, Q9, Q11, Q13: BC558; TO92-EBC
QP1, QP2, QP3, QP4, QP5, QP6: IRLZ44N; TO-220-3_Horizontal_TabUp
R10, R11, R12, R13, R14, R15, R16, R17, R18, R19, R20, R21: R_Small; R_Axial_DIN0207_L6.3mm_D2.5mm_P7.62mm_Horizontal

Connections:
/Inyectores/Encendido/INYL5A: R17.1
/Inyectores/Encendido/INYL6A: R21.1
ACC: Q2.C, Q4.C, Q6.C, Q8.C, Q10.C, Q12.C; also elsewhere on the board
GND: Q3.C, Q5.C, Q7.C, Q9.C, Q11.C, Q13.C; also elsewhere on the board
GND2: D6.A, D7.A, D8.A, D9.A, D10.A, D11.A, QP1.3 (S), QP2.3 (S), QP3.3 (S), QP4.3 (S), QP5.3 (S), QP6.3 (S); also elsewhere on the board
INY1: D6.C, QP1.2 (D); also elsewhere on the board
INY2: D8.C, QP3.2 (D); also elsewhere on the board
INY3: D10.C, QP5.2 (D); also elsewhere on the board
INY4: D7.C, QP2.2 (D); also elsewhere on the board
INY5: D9.C, QP4.2 (D); also elsewhere on the board
INY6: D11.C, QP6.2 (D); also elsewhere on the board
INYL1A: R12.1
INYL2A: R16.1
INYL3A: R20.1
INYL4A: R13.1
unnamed: Q2.B, Q3.B, R12.2
unnamed: Q2.E, Q3.E, R10.1
unnamed: Q4.B, Q5.B, R13.2
unnamed: Q4.E, Q5.E, R11.1
unnamed: Q6.B, Q7.B, R16.2
unnamed: Q6.E, Q7.E, R14.1
unnamed: Q8.B, Q9.B, R17.2
unnamed: Q8.E, Q9.E, R15.1
unnamed: Q10.B, Q11.B, R20.2
unnamed: Q10.E, Q11.E, R18.1
unnamed: Q12.B, Q13.B, R21.2
unnamed: Q12.E, Q13.E, R19.1
unnamed: QP1.1 (G), R10.2
unnamed: QP2.1 (G), R11.2
unnamed: QP3.1 (G), R14.2
unnamed: QP4.1 (G), R15.2
unnamed: QP5.1 (G), R18.2
unnamed: QP6.1 (G), R19.2

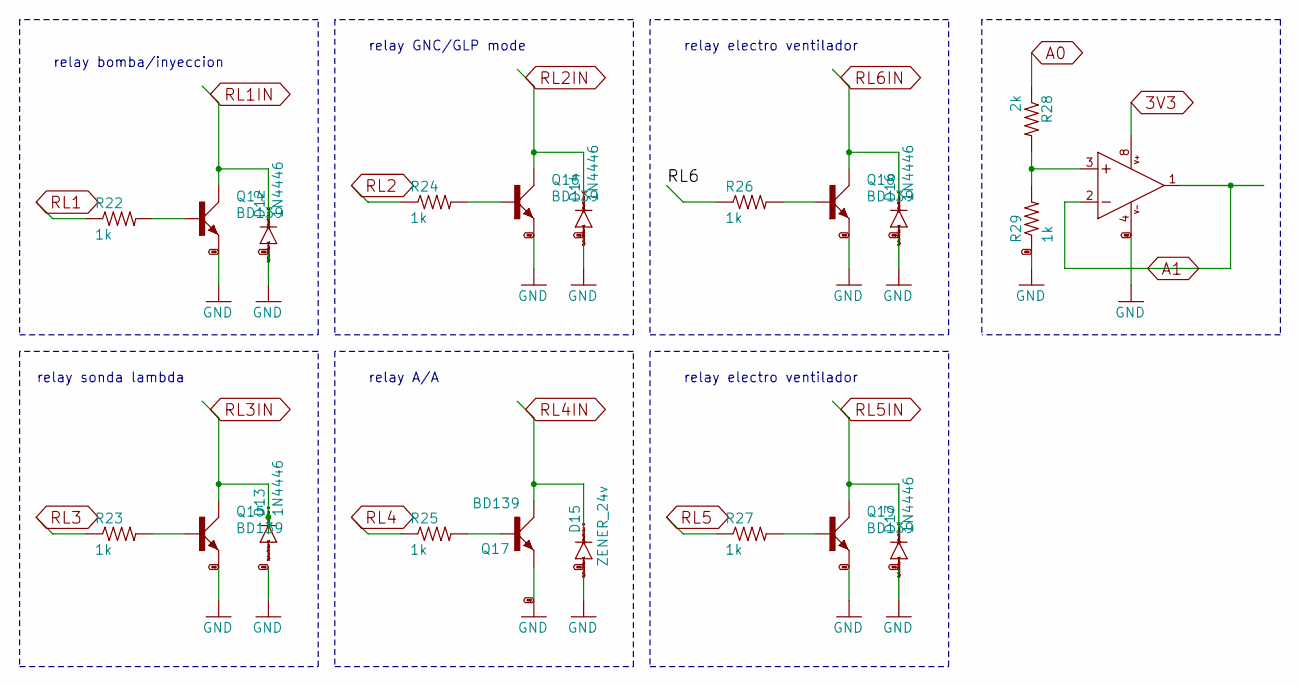
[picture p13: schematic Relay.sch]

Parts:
D12, D13, D14, D16, D17: 1N4446; DO35-10
D15: ZENER_24v; DO35-10
IC5: LM358D; SO08
Q14, Q15, Q16, Q17, Q18, Q19: BD139; TO126AV
R22, R23, R24, R25, R26, R27, R29: 1k; 0204_5
R28: 2k; 0204_5

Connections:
3V3: IC5.8 (V+); also elsewhere on the board
/Relay/RL6: R26.1
A0: R28.1; also elsewhere on the board
A1: IC5.1 (OUT), IC5.2 (-IN); also elsewhere on the board
GND: D12.A, D14.A, D15.A, D16.A, D17.A, IC5.4 (V-), Q14.E, Q15.E, Q16.E, Q17.E, Q18.E, Q19.E, R29.1; also elsewhere on the board
unnamed: IC5.3 (+IN), R28.2, R29.2
unnamed: Q14.B, R22.2
unnamed: Q15.B, R23.2
unnamed: Q16.B, R24.2
unnamed: Q17.B, R25.2
unnamed: Q18.B, R26.2
unnamed: Q19.B, R27.2
RL1: R22.1; also elsewhere on the board
RL1IN: D12.C, Q14.C; also elsewhere on the board
RL2: R24.1; also elsewhere on the board
RL2IN: D14.C, Q16.C; also elsewhere on the board
RL3: R23.1; also elsewhere on the board
RL3IN: D13.C, Q15.C; also elsewhere on the board
RL4: R25.1; also elsewhere on the board
RL4IN: D15.C, Q17.C; also elsewhere on the board
RL5: R27.1; also elsewhere on the board
RL5IN: D17.C, Q19.C; also elsewhere on the board
RL6IN: D16.C, Q18.C; also elsewhere on the board

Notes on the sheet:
relay bomba/inyeccion
relay GNC/GLP mode
relay sonda lambda
relay A/A
relay electro ventilador

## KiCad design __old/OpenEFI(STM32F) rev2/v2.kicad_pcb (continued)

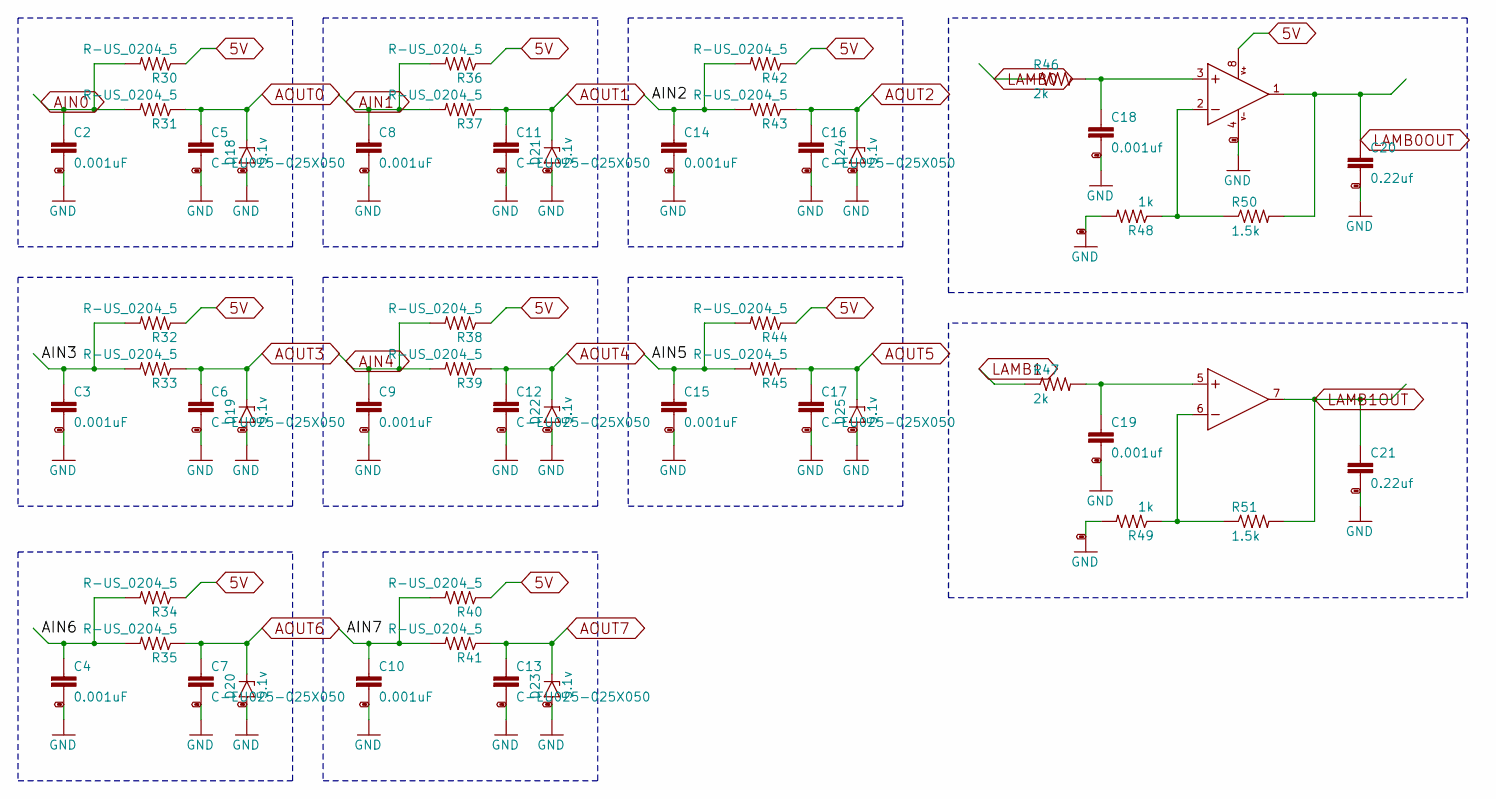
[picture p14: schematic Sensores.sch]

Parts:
C2, C3, C4, C8, C9, C10, C14, C15: 0.001uF; C025-025X050
C5, C6, C7, C11, C12, C13, C16, C17: C-EU025-025X050; C025-025X050
C18, C19: 0.001uf; C025-025X050
C20, C21: 0.22uf; C025-025X050
D18, D19, D20, D21, D22, D23, D24, D25: 5.1v; ZDIO-5
IC5, IC6: LM358D; SO08
R30, R31, R32, R33, R34, R35, R36, R37, R38, R39, R40, R41, R42, R43, R44, R45: R-US_0204_5; 0204_5
R46, R47: 2k; 0204_5
R48, R49: 1k; 0204_5
R50, R51: 1.5k; 0204_5

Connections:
5V: IC6.8 (V+), R30.1, R32.1, R34.1, R36.1, R38.1, R40.1, R42.1, R44.1; also elsewhere on the board
/Sensores/AIN2: C14.1, R42.2, R43.2
/Sensores/AIN3: C3.1, R32.2, R33.2
/Sensores/AIN5: C15.1, R44.2, R45.2
/Sensores/AIN6: C4.1, R34.2, R35.2
/Sensores/AIN7: C10.1, R40.2, R41.2
AIN0: C2.1, R30.2, R31.2
AIN1: C8.1, R36.2, R37.2
AIN4: C9.1, R38.2, R39.2
AOUT0: C5.1, D18.C, R31.1; also elsewhere on the board
AOUT1: C11.1, D21.C, R37.1; also elsewhere on the board
AOUT2: C16.1, D24.C, R43.1; also elsewhere on the board
AOUT3: C6.1, D19.C, R33.1; also elsewhere on the board
AOUT4: C12.1, D22.C, R39.1; also elsewhere on the board
AOUT5: C17.1, D25.C, R45.1; also elsewhere on the board
AOUT6: C7.1, D20.C, R35.1; also elsewhere on the board
AOUT7: C13.1, D23.C, R41.1; also elsewhere on the board
GND: C2.2, C3.2, C4.2, C5.2, C6.2, C7.2, C8.2, C9.2, C10.2, C11.2, C12.2, C13.2, C14.2, C15.2, C16.2, C17.2, C18.2, C19.2, C20.2, C21.2, D18.A, D19.A, D20.A, D21.A, D22.A, D23.A, D24.A, D25.A, IC6.4 (V-), R48.2, R49.2; also elsewhere on the board
LAMB0: R46.1
LAMB0OUT: C20.1, IC6.1 (OUT), R50.2; also elsewhere on the board
LAMB1: R47.1
LAMB1OUT: C21.1, IC5.7 (OUT), R51.2; also elsewhere on the board
unnamed: C18.1, IC6.3 (+IN), R46.2
unnamed: C19.1, IC5.5 (+IN), R47.2
unnamed: IC5.6 (-IN), R49.1, R51.1
unnamed: IC6.2 (-IN), R48.1, R50.1

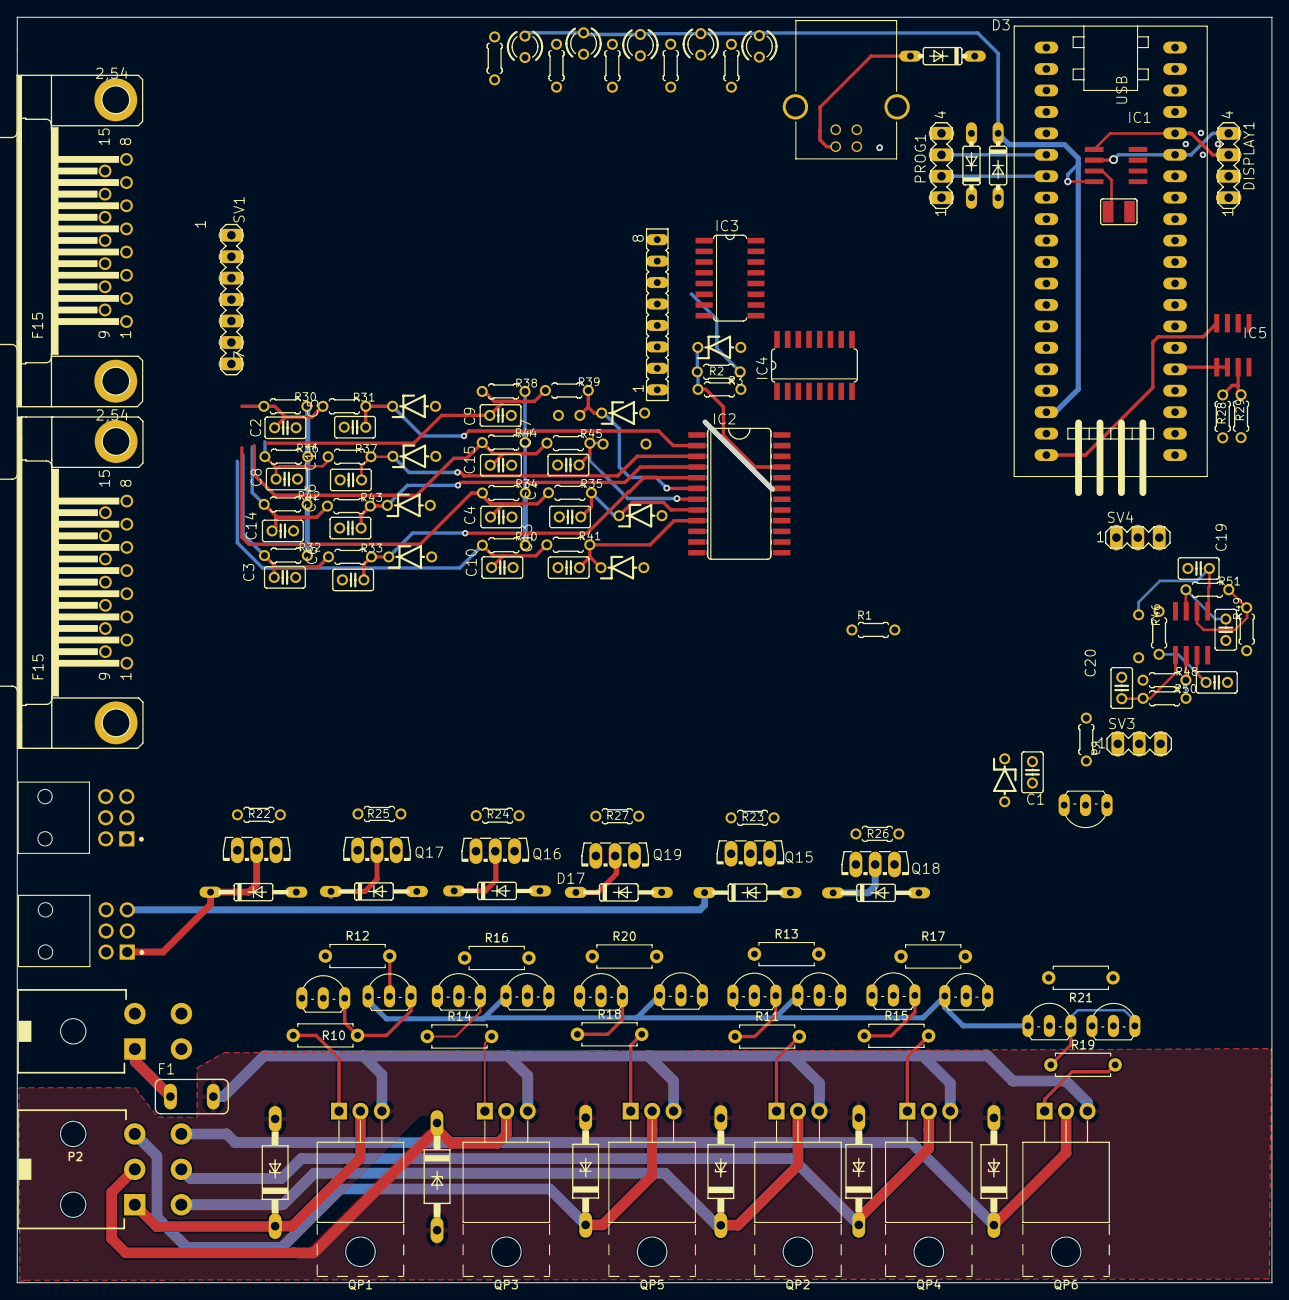
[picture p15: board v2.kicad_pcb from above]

Board: 4 copper layers, 148.6 x 149.9 mm, 149 parts (0 on the bottom side), 101 nets.

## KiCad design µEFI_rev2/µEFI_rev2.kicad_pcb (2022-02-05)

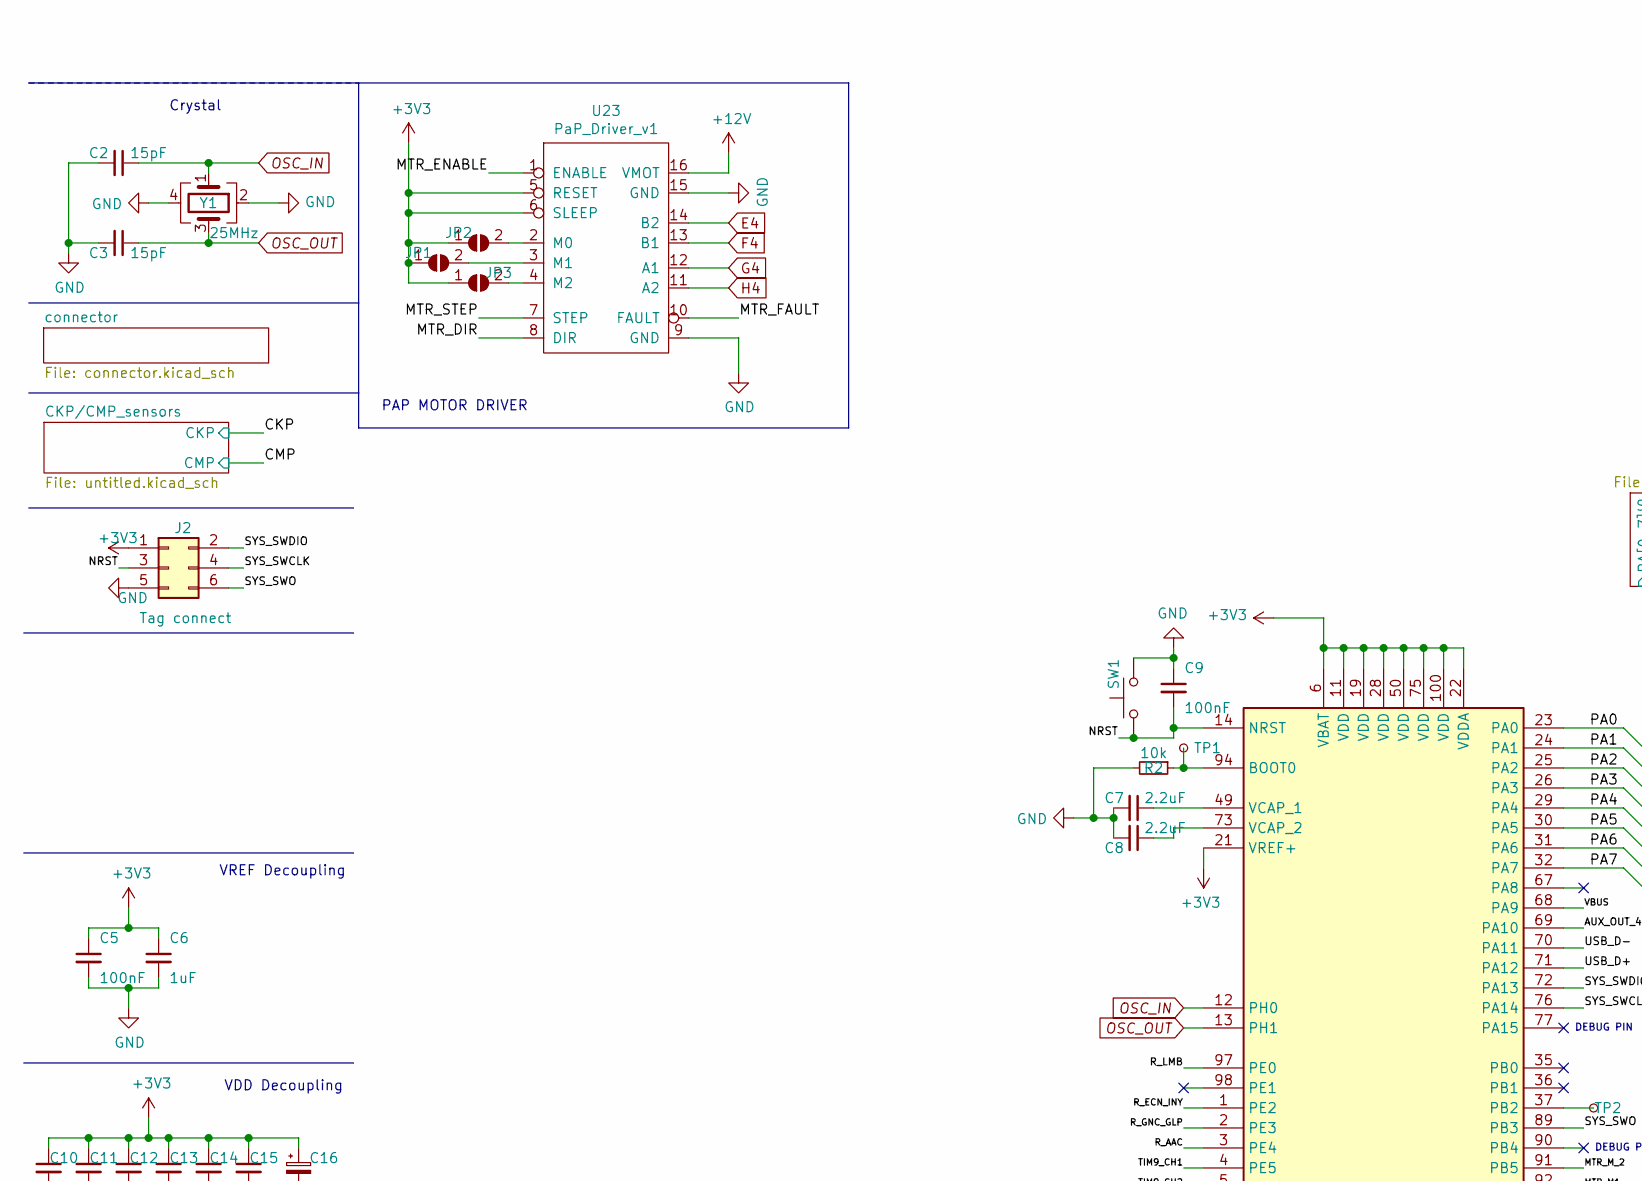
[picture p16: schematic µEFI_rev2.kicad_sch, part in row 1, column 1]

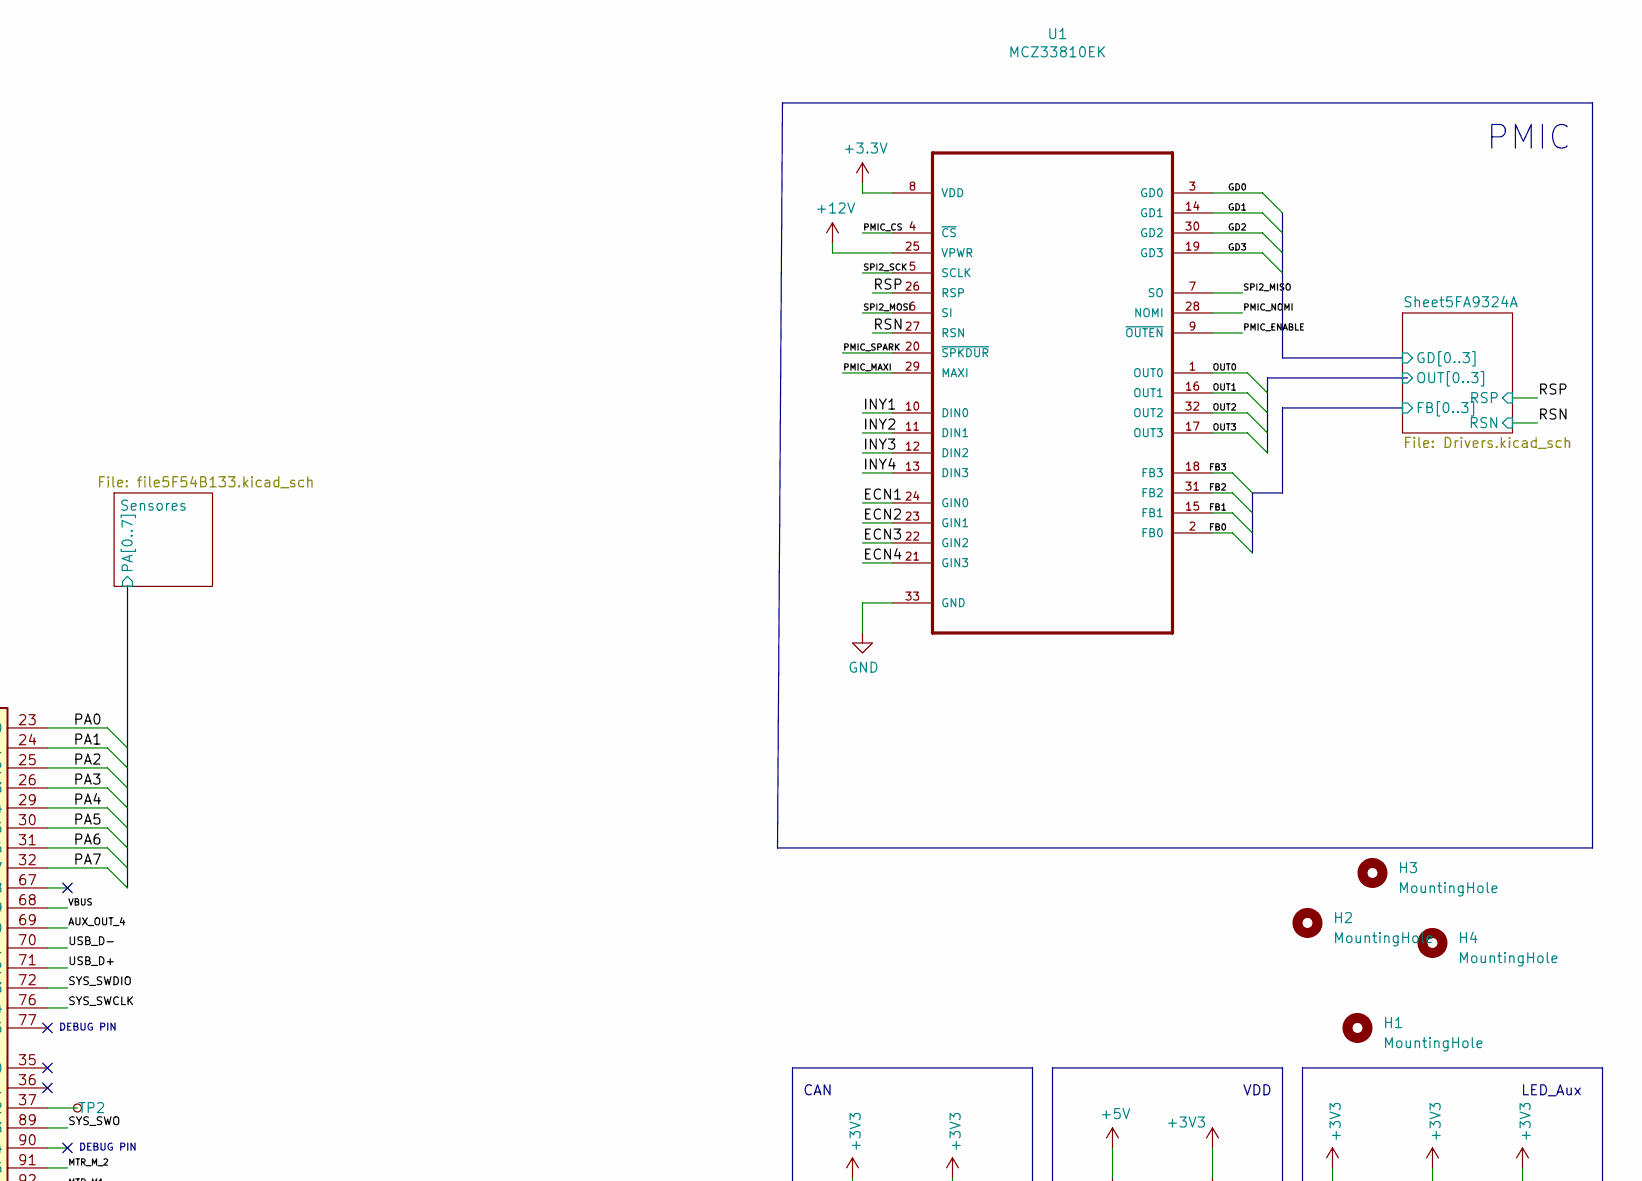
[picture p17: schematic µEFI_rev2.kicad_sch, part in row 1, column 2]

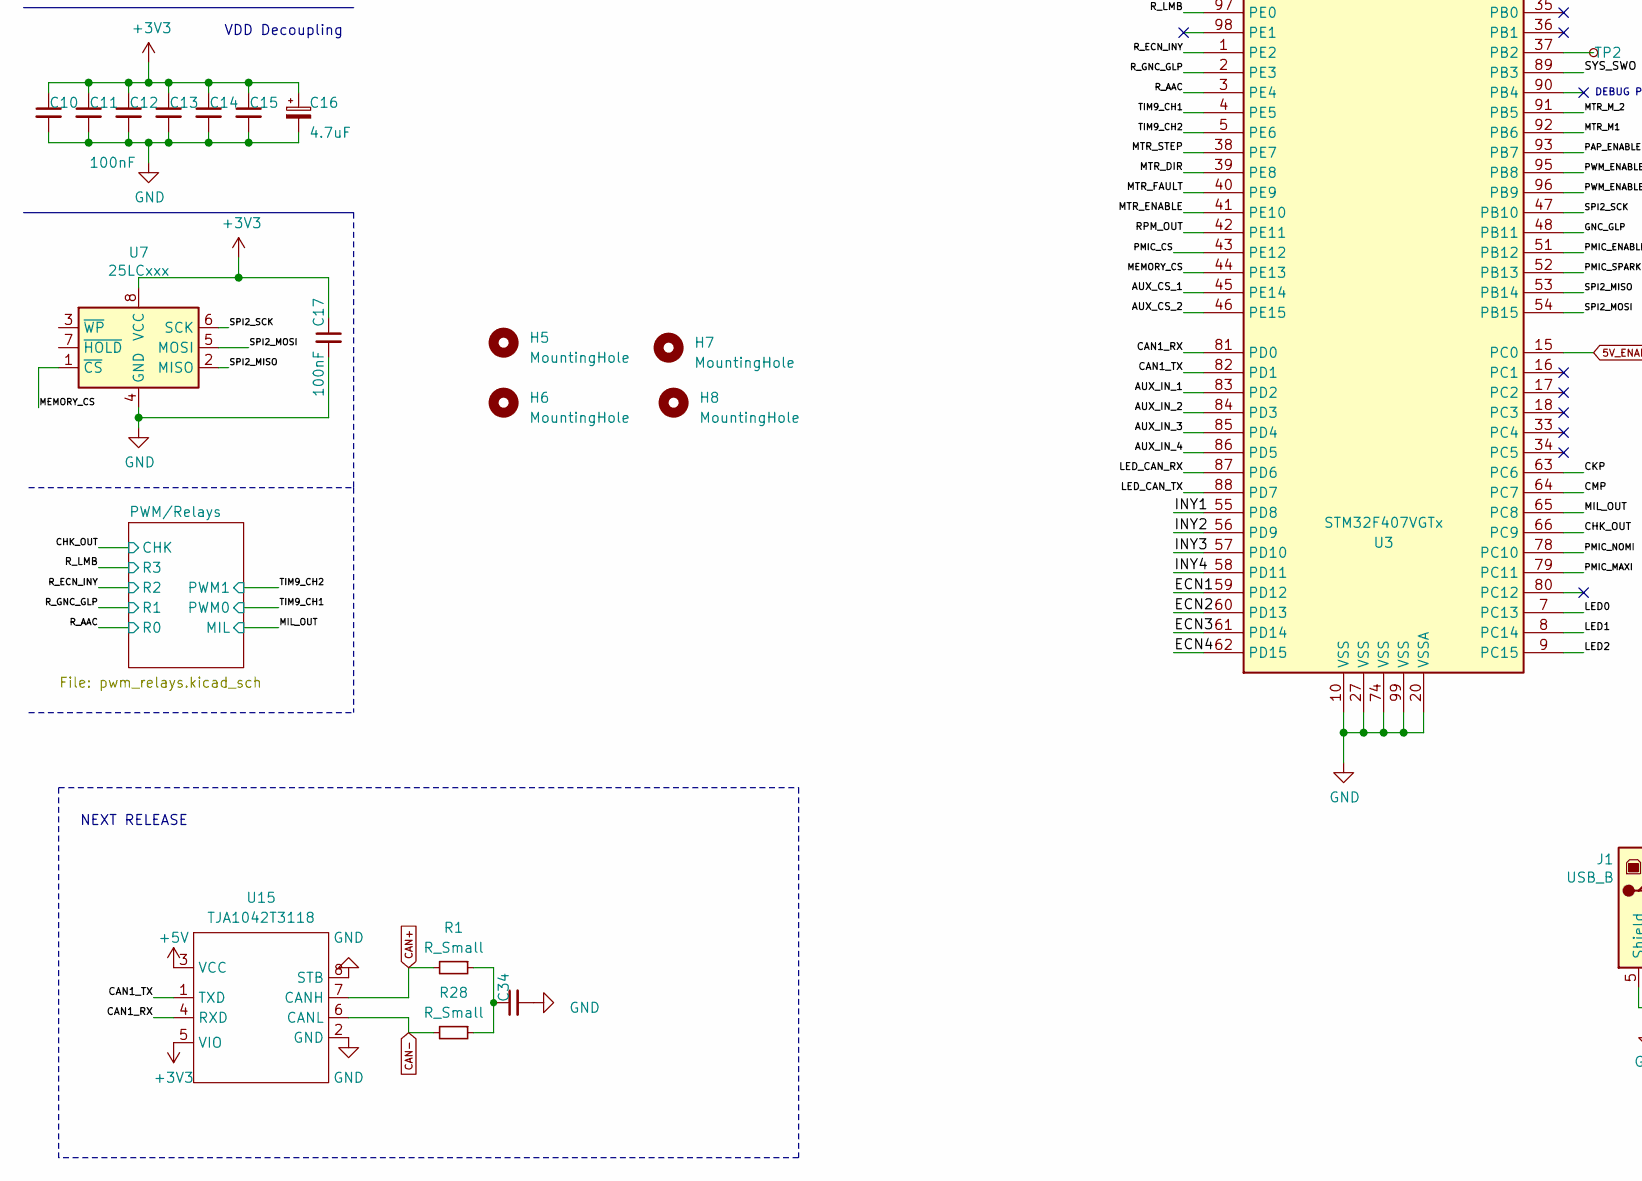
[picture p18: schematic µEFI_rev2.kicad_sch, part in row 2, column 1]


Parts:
C2, C3: 15pF; C_0805_2012Metric; LCSC C1794
C5, C9, C10, C11, C12, C13, C14, C15, C17: 100nF; C_0805_2012Metric; LCSC C49678
C6: 1uF; C_0805_2012Metric; LCSC C28323
C7, C8: 2.2uF; C_0805_2012Metric; LCSC C49217
C16: 4.7uF; C_0805_2012Metric; LCSC 0805
C34: 4.7nF; C_0805_2012Metric; LCSC C77475
D1, D5, D6, D7, D8, D9, D10, D12, D13: LED; LED_0603_1608Metric
H1, H2, H3, H4: MountingHole; MountingHole_2.2mm_M2_Pad_Via
H5, H6, H7, H8: MountingHole; TestPoint_Pad_D1.0mm
J1: USB_B; USB_B_OST_USB-B1HSxx_Horizontal
J2: Tag connect; Tag-Connect_TC2030-IDC-NL_2x03_P1.27mm_Vertical
JP1, JP2, JP3: SolderJumper_2_Open; SolderJumper-2_P1.3mm_Open_RoundedPad1.0x1.5mm
LOGO1: Logo_Open_Hardware_Large; OSHW-Logo2_14.6x12mm_SilkScreen
Q8, Q9: SS8050; SOT-23; LCSC C2150
R1, R28: R_Small; R_1206_3216Metric; LCSC C205298
R2: 10k; R_0603_1608Metric
R3, R4, R5, R24, R25, R26, R27, R29, R30: R_Small; R_0603_1608Metric
R31, R32: 1k; R_0603_1608Metric; LCSC C21190
SW1: SW_Push; SW_SPST_TL3342
SYM1: SYM_Hot_Small; KiCad-Logo2_6mm_SilkScreen
TP1: BOOT0; TestPoint_Pad_D2.0mm
TP2: BOOT1; TestPoint_Pad_D2.0mm
U1: MCZ33810EK; SOP65P1030X245-33N
U3: STM32F407VGTx; LQFP-100_14x14mm_P0.5mm
U7: 25LCxxx; SOIC-8_3.9x4.9mm_P1.27mm
U15: TJA1042T3118; HTSOP-8-1EP_3.9x4.9mm_P1.27mm_EP2.4x3.2mm
U23: PaP_Driver_v1; DIP-16_598_ELL
Y1: 25MHz; Crystal_SMD_3225-4Pin_3.2x2.5mm

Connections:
5V_ENABLE: U3.15 (PC0); also elsewhere on the board
+5V: D5.2 (A), U15.3 (VCC); also elsewhere on the board
+12V: U1.25 (VPWR), U23.16 (VMOT); also elsewhere on the board
/AUX_CS_1: U3.45 (PE14)
/AUX_CS_2: U3.46 (PE15)
/AUX_IN_1: U3.83 (PD2)
/AUX_IN_2: U3.84 (PD3)
/AUX_IN_3: U3.85 (PD4)
/AUX_IN_4: U3.86 (PD5)
/AUX_OUT_4: U3.69 (PA10)
/CAN1_RX: U3.81 (PD0), U15.4 (RXD)
/CAN1_TX: U3.82 (PD1), U15.1 (TXD)
/CHK: Q9.3 (C), R30.2
/CHK_OUT: R32.1, U3.66 (PC9); also elsewhere on the board
/CKP: U3.63 (PC6); also elsewhere on the board
/CMP: U3.64 (PC7); also elsewhere on the board
/ECN1: U1.24 (GIN0), U3.59 (PD12)
/ECN2: U1.23 (GIN1), U3.60 (PD13)
/ECN3: U1.22 (GIN2), U3.61 (PD14)
/ECN4: U1.21 (GIN3), U3.62 (PD15)
/GNC_GLP: U3.48 (PB11)
/INY1: U1.10 (DIN0), U3.55 (PD8)
/INY2: U1.11 (DIN1), U3.56 (PD9)
/INY3: U1.12 (DIN2), U3.57 (PD10)
/INY4: U1.13 (DIN3), U3.58 (PD11)
/LED0: R25.2, U3.7 (PC13)
/LED1: R26.2, U3.8 (PC14)
/LED2: R27.2, U3.9 (PC15)
/LED_CAN_RX: R24.2, U3.87 (PD6)
/LED_CAN_TX: R5.2, U3.88 (PD7)
/MEMORY_CS: U3.44 (PE13), U7.1 (~CS)
/MIL: Q8.3 (C), R29.2
/MIL_OUT: R31.1, U3.65 (PC8); also elsewhere on the board
/MTR_DIR: U3.39 (PE8), U23.8 (DIR)
/MTR_ENABLE: U3.41 (PE10), U23.1 (ENABLE)
/MTR_FAULT: U3.40 (PE9), U23.10 (FAULT)
/MTR_M1: U3.92 (PB6)
/MTR_M_2: U3.91 (PB5)
/MTR_STEP: U3.38 (PE7), U23.7 (STEP)
/NRST: C9.2, J2.3, SW1.1, U3.14 (NRST)
/PAP_ENABLE: U3.93 (PB7)
/PMIC_CS: U1.4 (~CS), U3.43 (PE12)
/PMIC_ENABLE: U1.9 (~OUTEN), U3.51 (PB12)
/PMIC_MAXI: U1.29 (MAXI), U3.79 (PC11)
/PMIC_NOMI: U1.28 (NOMI), U3.78 (PC10)
/PMIC_SPARK: U1.20 (~SPKDUR), U3.52 (PB13)
/PWM_ENABLE_1: U3.96 (PB9)
/PWM_ENABLE_2: U3.95 (PB8)
/RPM_OUT: U3.42 (PE11)
/RSN: U1.27 (RSN); also elsewhere on the board
/RSP: U1.26 (RSP); also elsewhere on the board
/R_AAC: U3.3 (PE4); also elsewhere on the board
/R_ECN_INY: U3.1 (PE2); also elsewhere on the board
/R_GNC_GLP: U3.2 (PE3); also elsewhere on the board
/R_LMB: U3.97 (PE0); also elsewhere on the board
/SPI2_MISO: U1.7 (SO), U3.53 (PB14), U7.2 (MISO)
/SPI2_MOSI: U1.6 (SI), U3.54 (PB15), U7.5 (MOSI)
/SPI2_SCK: U1.5 (SCLK), U3.47 (PB10), U7.6 (SCK)
/SYS_SWCLK: J2.4, U3.76 (PA14)
/SYS_SWDIO: J2.2, U3.72 (PA13)
/SYS_SWO: J2.6, U3.89 (PB3)
/Sensores/PA0: U3.23 (PA0); also elsewhere on the board
/Sensores/PA1: U3.24 (PA1); also elsewhere on the board
/Sensores/PA2: U3.25 (PA2); also elsewhere on the board
/Sensores/PA3: U3.26 (PA3); also elsewhere on the board
/Sensores/PA4: U3.29 (PA4); also elsewhere on the board
/Sensores/PA5: U3.30 (PA5); also elsewhere on the board
/Sensores/PA6: U3.31 (PA6); also elsewhere on the board
/Sensores/PA7: U3.32 (PA7); also elsewhere on the board
/Sheet5FA9324A/FB0: U1.2 (FB0); also elsewhere on the board
/Sheet5FA9324A/FB1: U1.15 (FB1); also elsewhere on the board
/Sheet5FA9324A/FB2: U1.31 (FB2); also elsewhere on the board
/Sheet5FA9324A/FB3: U1.18 (FB3); also elsewhere on the board
/Sheet5FA9324A/GD0: U1.3 (GD0); also elsewhere on the board
/Sheet5FA9324A/GD1: U1.14 (GD1); also elsewhere on the board
/Sheet5FA9324A/GD2: U1.30 (GD2); also elsewhere on the board
/Sheet5FA9324A/GD3: U1.19 (GD3); also elsewhere on the board
/TIM9_CH1: U3.4 (PE5); also elsewhere on the board
/TIM9_CH2: U3.5 (PE6); also elsewhere on the board
/USB_D+: J1.3 (D+), U3.71 (PA12)
/USB_D-: J1.2 (D-), U3.70 (PA11)
/VBUS: J1.1 (VBUS), U3.68 (PA9)
CAN+: R1.2, U15.7 (CANH); also elsewhere on the board
CAN-: R28.2, U15.6 (CANL); also elsewhere on the board
E4: U23.14 (B2); also elsewhere on the board
F4: U23.13 (B1); also elsewhere on the board
G4: U23.12 (A1); also elsewhere on the board
H4: U23.11 (A2); also elsewhere on the board
L3: U1.32 (OUT2); also elsewhere on the board
L4: U1.17 (OUT3); also elsewhere on the board
M3: U1.1 (OUT0); also elsewhere on the board
M4: U1.16 (OUT1); also elsewhere on the board
unnamed: C7.1, U3.49 (VCAP_1)
unnamed: C8.1, U3.73 (VCAP_2)
unnamed: C34.1, R1.1, R28.1
unnamed: D1.1 (K), R3.1
unnamed: D5.1 (K), R4.1
unnamed: D6.1 (K), R5.1
unnamed: D7.1 (K), R24.1
unnamed: D8.1 (K), R25.1
unnamed: D9.1 (K), R26.1
unnamed: D10.1 (K), R27.1
unnamed: D12.1 (K), R29.1
unnamed: D13.1 (K), R30.1
unnamed: JP1.2 (B), U23.3 (M1)
unnamed: JP2.2 (B), U23.2 (M0)
unnamed: JP3.2 (B), U23.4 (M2)
unnamed: Q8.1 (B), R31.2
unnamed: Q9.1 (B), R32.2
unnamed: R2.1, TP1.1, U3.94 (BOOT0)
unnamed: TP2.1, U3.37 (PB2)
OSC_IN: C2.1, U3.12 (PH0), Y1.1
OSC_OUT: C3.1, U3.13 (PH1), Y1.3

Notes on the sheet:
Crystal
NEXT RELEASE
VREF Decoupling
VDD Decoupling
PAP MOTOR DRIVER
DEBUG PIN
CAN
VDD
PMIC
LED_Aux


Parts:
C52, C53, C54, C55, C56, C57: 0.01uF; C_0603_1608Metric; LCSC C100042
JP23, JP24: SolderJumper_2_Open; SolderJumper-2_P1.3mm_Open_RoundedPad1.0x1.5mm
R81, R112, R113, R114, R115, R116, R117, R118, R119, R120: 4.99K 1/2W; R_1210_3225Metric; LCSC C407178
R121, R122: R_Small; R_0603_1608Metric
TP3, TP4, TP5, TP6, TP7, TP8: TestPoint; TestPoint_Pad_1.0x1.0mm
U36: MAX9926UAEE+; SOP63P602X175-16N

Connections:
/CKP: R121.2, TP8.1, U36.4 (COUT1); also elsewhere on the board
/CKP/CMP_sensors/IN1+: C54.1, R113.2, R115.1, TP4.1, U36.16 (IN1+)
/CKP/CMP_sensors/IN1-: C54.2, JP23.1 (A), R114.2, TP5.1, U36.15 (IN1-)
/CKP/CMP_sensors/IN2+: C57.2, JP24.1 (A), R119.2, TP6.1, U36.10 (IN2-)
/CKP/CMP_sensors/IN2-: C57.1, R118.2, R120.1, TP3.1, U36.9 (IN2+)
/CMP: R122.2, TP7.1, U36.5 (COUT2); also elsewhere on the board
CKP+: C55.1, R117.1; also elsewhere on the board
CKP-: C56.1, R116.1; also elsewhere on the board
CMP+: C53.1, R81.1; also elsewhere on the board
CMP-: C52.1, R112.1; also elsewhere on the board
unnamed: JP23.2 (B), R115.2
unnamed: JP24.2 (B), R120.2
unnamed: R112.2, R114.1
unnamed: R81.2, R113.1
unnamed: R116.2, R118.1
unnamed: R117.2, R119.1


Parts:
U20, U22: TPL7407LAPWR; TSSOP-16_4.4x5mm_P0.65mm

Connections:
+12V: U20.9 (COM), U22.9 (COM); also elsewhere on the board
/CHK_OUT: U20.6 (IN6); also elsewhere on the board
/MIL_OUT: U20.7 (IN7); also elsewhere on the board
/R_AAC: U22.1 (IN1), U22.2 (IN2); also elsewhere on the board
/R_ECN_INY: U22.5 (IN5), U22.6 (IN6); also elsewhere on the board
/R_GNC_GLP: U22.3 (IN3), U22.4 (IN4); also elsewhere on the board
/R_LMB: U22.7 (IN7); also elsewhere on the board
/TIM9_CH1: U20.1 (IN1), U20.2 (IN2), U20.3 (IN3); also elsewhere on the board
/TIM9_CH2: U20.4 (IN4), U20.5 (IN5); also elsewhere on the board
B4: U20.12 (OUT5), U20.13 (OUT4); also elsewhere on the board
C4: U20.14 (OUT3), U20.15 (OUT2), U20.16 (OUT1); also elsewhere on the board
D3: U20.10 (OUT7); also elsewhere on the board
D4: U22.11 (OUT6), U22.12 (OUT5); also elsewhere on the board
E3: U20.11 (OUT6); also elsewhere on the board
F3: U22.10 (OUT7); also elsewhere on the board
G3: U22.13 (OUT4), U22.14 (OUT3); also elsewhere on the board
H3: U22.15 (OUT2), U22.16 (OUT1); also elsewhere on the board

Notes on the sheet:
CONNECTOR BIND
SCH BIND


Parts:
C49, C51: 240pF; C_0603_1608Metric; LCSC C185593
D14, D18: DZ2S033X0L; D_MiniMELF; LCSC C8056
JP11, JP15, JP17, JP18, JP19: Jumper_NC_Small; SolderJumper-2_P1.3mm_Open_TrianglePad1.0x1.5mm
R82: 100k 1/10W +-1%; R_0603_1608Metric; LCSC C217840
R83: 20k 1/10W +-1%; R_0603_1608Metric
R87: 3.32k +-1%; R_0603_1608Metric; LCSC C234508
R92: 28.6k +-1%; R_0603_1608Metric; LCSC C217931
R97: 2.2k; R_0603_1608Metric; LCSC C309092
R108, R109: 10k; R_0603_1608Metric
U2, U8, U9, U10, U11, U12, U13, U14: SensorsV2; Sensors_v2
U27, U31: LM321; SOT-23-5

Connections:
+5V: R92.2, U27.5 (V+); also elsewhere on the board
+12V: U2.2 (12v), U8.2 (12v), U9.2 (12v), U10.2 (12v), U11.2 (12v), U12.2 (12v), U13.2 (12v), U14.2 (12v), U31.5 (V+); also elsewhere on the board
+12VA: R82.2; also elsewhere on the board
/Sensores/PA0: U2.4 (AOUT); also elsewhere on the board
/Sensores/PA1: U8.4 (AOUT); also elsewhere on the board
/Sensores/PA2: U9.4 (AOUT); also elsewhere on the board
/Sensores/PA3: U10.4 (AOUT); also elsewhere on the board
/Sensores/PA4: U11.4 (AOUT); also elsewhere on the board
/Sensores/PA5: U12.4 (AOUT); also elsewhere on the board
/Sensores/PA6: U13.4 (AOUT); also elsewhere on the board
/Sensores/PA7: U14.4 (AOUT); also elsewhere on the board
/Sensores/PC0: JP19.2
/Sensores/PC5: JP11.2
B1: C49.1, R87.1, R92.1, R97.2; also elsewhere on the board
C1: U13.3 (AIN); also elsewhere on the board
D1: U11.3 (AIN); also elsewhere on the board
E1: U8.3 (AIN); also elsewhere on the board
F1: U12.3 (AIN); also elsewhere on the board
G1: U14.3 (AIN); also elsewhere on the board
H1: U9.3 (AIN); also elsewhere on the board
J1: U10.3 (AIN); also elsewhere on the board
K1: U2.3 (AIN); also elsewhere on the board
unnamed: C51.1, D14.1 (K), R82.1, R83.1, U27.1 (+)
unnamed: D18.1 (K), JP15.2, JP18.1, JP19.1, U31.4
unnamed: JP11.1, U27.3 (-), U27.4
unnamed: JP15.1, JP17.1, U31.3 (-)
unnamed: JP17.2, R108.2
unnamed: JP18.2, R108.1, R109.2
unnamed: R97.1, U31.1 (+)

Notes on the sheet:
TEMP
TPS
AIR_TEMP
PRES_FUEL
PRES_OIL
TODO: VBAT
Solo en puentear si no te utiliza una wideband

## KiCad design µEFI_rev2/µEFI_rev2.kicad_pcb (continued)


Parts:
C18, C19, C20, C21: 10pF; C_0603_1608Metric; LCSC C106245
C22: 10pF; C_0603_1608Metric
C23, C24, C25, C26, C27, C28, C29, C30: 10nF; C_0603_1608Metric; LCSC C100042
Q1, Q2, Q3, Q4: ISL9V5045S3ST; TO-263-2
R6, R7: 100R; R_0603_1608Metric; LCSC C159890
R8: 0.02R; R_2512_6332Metric; LCSC C326611
R9, R10, R11, R12: 4.02k; R_0603_1608Metric; LCSC C23040
R13, R14, R15, R16: 36K; R_0603_1608Metric; LCSC C192548

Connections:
/RSN: R6.2; also elsewhere on the board
/RSP: R7.2; also elsewhere on the board
/Sheet5FA9324A/FB0: C18.2, R9.2, R13.1; also elsewhere on the board
/Sheet5FA9324A/FB1: C19.2, R10.2, R14.1; also elsewhere on the board
/Sheet5FA9324A/FB2: C20.2, R11.2, R15.1; also elsewhere on the board
/Sheet5FA9324A/FB3: C21.2, R12.2, R16.1; also elsewhere on the board
/Sheet5FA9324A/GD0: Q2.1 (G); also elsewhere on the board
/Sheet5FA9324A/GD1: Q1.1 (G); also elsewhere on the board
/Sheet5FA9324A/GD2: Q3.1 (G); also elsewhere on the board
/Sheet5FA9324A/GD3: Q4.1 (G); also elsewhere on the board
L1: C20.1, C23.1, Q3.2 (C), R15.2; also elsewhere on the board
L2: C21.1, C24.1, Q4.2 (C), R16.2; also elsewhere on the board
L3: C28.2; also elsewhere on the board
L4: C27.2; also elsewhere on the board
M1: C18.1, C25.1, Q2.2 (C), R13.2; also elsewhere on the board
M2: C19.1, C26.1, Q1.2 (C), R14.2; also elsewhere on the board
M3: C30.2; also elsewhere on the board
M4: C29.2; also elsewhere on the board
unnamed: C22.2, Q1.3 (E), Q2.3 (E), Q3.3 (E), Q4.3 (E), R7.1, R8.1


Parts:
C31: 100uF ±20% 35V; CP_Elec_6.3x7.7; LCSC C141427
C33: 47nF; C_0603_1608Metric
C36: 100nF; C_0805_2012Metric; LCSC C49678
D2, D3: 1N4148; D_SOD-523; LCSC C511874
D4: SMAJ58CA; D_SMA
J3: 36638-0002; 366380002; Manufacturer_Part_Number 36638-0002; Mouser Part Number 538-36638-0002
J6: 1241434-1; TE_1241434-1; PARTREV C15
JP4: Jumper_NO_Small; SolderJumper-2_P1.3mm_Open_RoundedPad1.0x1.5mm
Q5: SS8050; SOT-23; LCSC C2150
Q6, Q7: IRLZ44N; TO-220-3_Vertical
Q10: IRF540N; TO-220-3_Vertical
R17: 10K 1/10W; R_0603_1608Metric
R18, R20, R33: 10R 1/10W; R_0603_1608Metric
R19: 1M 1/10W; R_0603_1608Metric
R21: 0.01R; R_1210_3225Metric; LCSC C175884
R22: 57.6K 1/10W; R_0603_1608Metric
R23: 4.99K 1/10W; R_0603_1608Metric
U4: MIC2940A-3.3WU; TO-263-3_TabPin2
U5: MIC2940A-5.0WT; TO-220-3_Vertical
U6: LT4363IMS; MSOP-12_3x4mm_P0.65mm

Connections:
5V_ENABLE: R33.1; also elsewhere on the board
+5V: Q10.3 (S), U5.3 (OUT); also elsewhere on the board
+12V: JP4.2, R21.1, R22.1, U4.1 (IN), U5.1 (IN), U6.2 (OUT); also elsewhere on the board
+12VA: D2.2 (A), J3.A4, JP4.1, Q5.2 (E), Q6.3 (S); also elsewhere on the board
A1: J3.A1
B1: J3.B1; also elsewhere on the board
B4: J3.B4; also elsewhere on the board
C1: J3.C1; also elsewhere on the board
C4: J3.C4; also elsewhere on the board
CAN+: J3.J2; also elsewhere on the board
CAN-: J3.K2; also elsewhere on the board
CKP+: J3.K4; also elsewhere on the board
CKP-: J3.J4; also elsewhere on the board
CMP+: J3.K3; also elsewhere on the board
CMP-: J3.J3; also elsewhere on the board
D1: J3.D1; also elsewhere on the board
D3: J3.D3; also elsewhere on the board
D4: J3.D4; also elsewhere on the board
E1: J3.E1; also elsewhere on the board
E3: J3.E3; also elsewhere on the board
E4: J3.E4; also elsewhere on the board
F1: J3.F1; also elsewhere on the board
F3: J3.F3; also elsewhere on the board
F4: J3.F4; also elsewhere on the board
G1: J3.G1; also elsewhere on the board
G3: J3.G3; also elsewhere on the board
G4: J3.G4; also elsewhere on the board
H1: J3.H1; also elsewhere on the board
H3: J3.H3; also elsewhere on the board
H4: J3.H4; also elsewhere on the board
J1: J3.J1; also elsewhere on the board
K1: J3.K1; also elsewhere on the board
L1: J3.L1; also elsewhere on the board
L2: J3.L2; also elsewhere on the board
L3: J3.L3; also elsewhere on the board
L4: J3.L4; also elsewhere on the board
M1: J3.M1; also elsewhere on the board
M2: J3.M2; also elsewhere on the board
M3: J3.M3; also elsewhere on the board
M4: J3.M4; also elsewhere on the board
unnamed: C33.1, R19.1, R20.2, U6.4 (GATE)
unnamed: C36.1, U6.12 (TMR)
unnamed: D2.1 (K), Q5.1 (B), R17.1
unnamed: D3.1 (K), R17.2
unnamed: Q5.3 (C), R18.2, R19.2
unnamed: Q6.1 (G), R18.1
unnamed: Q7.1 (G), R20.1
unnamed: Q10.1 (G), R33.2
unnamed: R22.2, R23.2, U6.1 (FB)

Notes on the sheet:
BYPASS SURGE PROTECTION
change to 0.01uf?

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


Board: 4 copper layers, 99.9 x 99.3 mm, 169 parts (43 on the bottom side), 157 nets.

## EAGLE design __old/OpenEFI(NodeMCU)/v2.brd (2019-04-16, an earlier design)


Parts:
BMP180: FE05-1
C9, C11: C-EU025-025X050; C025-025X050
C10: 0.001uF; C025-025X050
C12, C14, C16, C18: 0.001uf; C025-025X050
C13, C15: 0.1uf; C025-025X050
C17, C19: 0.22uf; C025-025X050
D1, D2, D3, D4, D5, D6, D7, D8, D16, D17, D18, D19: 1N4004; DO41-10
D9, D10, D11: 5.1v; ZDIO-5
D12, D13, D14, D15, D20, D21, D22, D23, D24, D25, D26, D27, D28, D29, D30, D31: S1M; SMA
D32: ZENER-DIODEZD-2.5; ZDIO-2.5
IC1: LOLINV3
IC2, IC5, IC9, IC10: LM358D; SO08
IC3, IC6: 74HC164D; SO14
IC7: 4051D; SO16
IC8: 24AA08SN; SO-08
IC11: L293D; DIL16
Q1, Q3, Q5, Q7, Q11, Q13: Aod442; TO252
Q2, Q4, Q6, Q8, Q12, Q14: BC858ASMD; SOT23-BEC
Q9, Q10, Q15, Q16: MJD122; DPAK
Q17, Q18, Q20: BSS138; SOT23
R1, R2, R3, R4, R18, R19: R-EU_0204/7; 0204/7
R5, R25, R28: 2k; 0204/5
R6, R13, R27, R30: 1.5k; 0204/5
R7: 15k; 0204/5
R8: 5k; 0204/5
R9, R10: R-US_0204/5; 0204/5
R11, R14: 2.2k; 0204/5
R12, R15: 3k; 0204/5
R16, R17, R20, R23, R26, R29: 1k; 0204/5
R21: 47k; 0204/5
R22: 91k; 0204/5
R24, R31, R32, R33, R34, R35: 10k; 0204/5
SJ1: SJW
SV1: MA07-1
T1, T2, T3, T4, T5, T6: BC848; SOT23
U$1: DC-DC-STEP-DOWN-LM2596
X1: F37HP

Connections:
3V: IC1.3 (3V), Q17.1 (G), Q18.1 (G), Q20.1 (G), R24.1, R32.1, R34.1
5V: BMP180.5, IC1.VIN, IC2.8 (V+), IC3.14 (VCC), IC5.8 (V+), IC6.14 (VCC), IC7.16 (VCC), IC8.8 (VCC), IC9.8 (V+), IC10.8 (V+), IC11.1 (1-2EN), IC11.9 (3-4EN), IC11.16 (VCC1), R10.1, R12.2, R15.2, R31.2, R33.2, R35.2, SV1.7, U$1.OUT+, X1.20, X1.21, X1.22, X1.24
A: IC1.SO, IC7.11 (A)
A0: IC2.3 (+IN), IC7.3 (X)
A1: IC1.A0, IC2.6 (-IN), IC2.7 (OUT)
ACC: D2.C, D3.C, D5.C, D8.C, D13.C, D15.C, D17.C, D19.C, D21.C, D23.C, D25.C, D27.C, D29.C, D31.C, IC11.8 (VCC2), R7.2, T1.3 (C), T2.3 (C), T3.3 (C), T4.3 (C), T5.3 (C), T6.3 (C), U$1.IN+, X1.1, X1.19
AIRIN: C10.1, R9.2, R10.2, X1.5
AIROUT: C11.1, D9.C, IC7.15 (X2), R9.1
B: IC1.SK, IC7.10 (B)
C: IC1.D0, IC7.9 (C)
CAN: IC1.D4, SV1.5
CKPIN: R5.1, X1.4
CKPOUT: IC1.D3, R13.2
CLK1: IC1.S2, IC3.8 (CLK), IC6.8 (CLK)
CLR1: IC1.S1, IC3.9 (CLR), IC6.9 (CLR)
CPKOUT: IC5.1 (OUT), IC5.2 (-IN), R13.1
DATA: IC1.S3, IC6.1 (A), IC6.2 (B)
DATA2: IC1.SC, IC3.1 (A), IC3.2 (B)
ECN1: D16.C, D17.A, Q11.2 (C), X1.14, X1.33
ECN1L: IC3.10 (QE), R18.2
ECN2: D18.C, D19.A, Q13.2 (C), X1.13, X1.32
ECN2L: IC3.11 (QF), R19.2
GND: BMP180.4, C9.2, C10.2, C11.2, C12.2, C13.2, C14.2, C15.2, C16.2, C17.2, C18.2, C19.2, D1.A, D4.A, D6.A, D7.A, D9.A, D10.A, D11.A, D12.A, D14.A, D16.A, D18.A, D20.A, D22.A, D24.A, D26.A, D28.A, D30.A, D32.A, IC1.GND, IC1.GND1, IC1.GND2, IC1.GND3, IC1.GND4, IC2.4 (V-), IC3.7 (GND), IC5.4 (V-), IC6.7 (GND), IC7.6 (INH), IC7.7 (VEE), IC7.8 (GND), IC8.1 (A0), IC8.2 (A1), IC8.3 (A2), IC8.4 (GND), IC9.4 (V-), IC10.4 (V-), IC11.4 (GND1), IC11.5 (GND2), IC11.12 (GND4), IC11.13 (GND3), Q1.3 (E), Q2.C, Q3.3 (E), Q4.C, Q5.3 (E), Q6.C, Q7.3 (E), Q8.C, Q9.3 (E), Q10.3 (E), Q11.3 (E), Q12.C, Q13.3 (E), Q14.C, Q15.3 (E), Q16.3 (E), R8.1, R22.2, R26.2, R29.2, SJ1.2, SV1.6, U$1.IN-, U$1.OUT-, X1.23, X1.25, X1.26
IAC_A: D24.C, D25.A, IC11.3 (1Y), X1.11
IAC_B: D26.C, D27.A, IC11.6 (2Y), X1.30
IAC_C: D28.C, D29.A, IC11.14 (4Y), X1.12
IAC_D: D30.C, D31.A, IC11.11 (3Y), X1.31
IAC_LA: IC6.12 (QG), IC11.2 (1A)
IAC_LB: IC6.13 (QH), IC11.7 (2A)
IAC_LC: IC6.10 (QE), IC11.15 (4A)
IAC_LD: IC6.11 (QF), IC11.10 (3A)
INY1: D1.C, D2.A, Q1.2 (C), X1.18, X1.37
INY2: D3.A, D4.C, Q3.2 (C), X1.17, X1.36
INY3: D5.A, D6.C, Q5.2 (C), X1.16, X1.35
INY4: D7.C, D8.A, Q7.2 (C), X1.15, X1.34
INYL1A: IC3.3 (QA), R1.2
INYL2A: IC3.4 (QB), R2.2
INYL3A: IC3.5 (QC), R3.2
INYL4A: IC3.6 (QD), R4.2
LAMB0: R25.1, X1.7
LAMB0OUT: C17.1, IC7.1 (X4), IC9.1 (OUT), R27.2
LAMB1: R28.1, X1.6
LAMB1OUT: C19.1, IC7.5 (X5), IC10.1 (OUT), R30.2
LED1: X1.10
LED2: X1.29
MISO: IC1.D6, Q17.2 (S), R32.2
MISO5V: Q17.3 (D), R33.1, SV1.4
MOSI: IC1.D7, Q18.2 (S), R34.2
MOSI5V: Q18.3 (D), R35.1, SV1.3
unnamed: C18.1, IC10.3 (+IN), R28.2
unnamed: Q1.1 (G), Q2.E, T2.2 (E)
unnamed: Q2.B, R1.1, T2.1 (B)
unnamed: Q9.1 (B), R16.2
unnamed: IC5.3 (+IN), R6.2
unnamed: C9.1, R5.2, R6.1
unnamed: Q10.1 (B), R17.2
unnamed: Q3.1 (G), Q4.E, T1.2 (E)
unnamed: Q4.B, R2.1, T1.1 (B)
unnamed: D32.C, IC2.5 (+IN), R21.2, R22.1
unnamed: Q11.1 (G), Q12.E, T5.2 (E)
unnamed: IC2.1 (OUT), IC2.2 (-IN), R21.1
unnamed: Q12.B, R18.1, T5.1 (B)
unnamed: Q5.1 (G), Q6.E, T3.2 (E)
unnamed: Q6.B, R3.1, T3.1 (B)
unnamed: Q15.1 (B), R20.2
unnamed: Q13.1 (G), Q14.E, T6.2 (E)
unnamed: Q14.B, R19.1, T6.1 (B)
unnamed: Q7.1 (G), Q8.E, T4.2 (E)
unnamed: Q8.B, R4.1, T4.1 (B)
unnamed: Q16.1 (B), R23.2
unnamed: C16.1, IC9.3 (+IN), R25.2
unnamed: IC9.2 (-IN), R26.1, R27.1
unnamed: IC8.7 (WP), SJ1.1
unnamed: IC10.2 (-IN), R29.1, R30.1
RL1: IC6.3 (QA), R16.1
RL1IN: D12.C, D13.A, Q9.4 (C), X1.27
RL2: IC6.4 (QB), R17.1
RL2IN: D14.C, D15.A, Q10.4 (C), X1.28
RL3: IC6.5 (QC), R20.1
RL3IN: D20.C, D21.A, Q15.4 (C), X1.8
RL4: IC6.6 (QD), R23.1
RL4IN: D22.C, D23.A, Q16.4 (C), X1.9
SCL: BMP180.2, IC1.D2, IC8.6 (SCL)
SCLK: IC1.D5, Q20.2 (S), R24.2
SCLK5V: Q20.3 (D), R31.1, SV1.2
SDA: BMP180.3, IC1.D1, IC8.5 (SDA)
TEMPIN: C14.1, R14.1, R15.1, X1.3
TEMPOUT: C15.1, D11.C, IC7.14 (X1), R14.2
TPSIN: C12.1, R11.1, R12.1, X1.2
TPSOUT: C13.1, D10.C, IC7.13 (X0), R11.2
VBAT: IC7.12 (X3), R7.1, R8.2

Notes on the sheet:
relay inyeccion
relay GNC/GLP
relay sonda lambda
relay A/A



Board: 2 copper layers, 160.0 x 100.0 mm, 118 parts (3 on the bottom side), 89 nets.

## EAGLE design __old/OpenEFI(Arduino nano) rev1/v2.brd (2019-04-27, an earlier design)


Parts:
ARDUINO_NANO1: ARDUINO_NANO
C3, C12, C14, C16, C18: 0.001uf; C025-025X050
C4, C13, C15: 0.1uf; C025-025X050
C5, C10: 0.001uF; C025-025X050
C6, C11: C-EU025-025X050; C025-025X050
C17, C19: 0.22uf; C025-025X050
D1, D4, D6, D7, D16, D18: 1N4004; DO41-10
D9, D10, D11, D25, D26, D27: 5.1v; ZDIO-5
D12, D13, D14, D15, D20, D21, D22, D23, D32, D33: S1M; SMA
IC1: 4050N; DIL16
IC6: 74HC164D; SO14
IC7: 4051D; SO16
IC8: 24AA08SN; SO-08
IC9, IC10: LM358D; SO08
P1: 39-30-06; 39-30-?06?
Q1, Q3, Q5, Q7, Q9, Q10, Q11, Q13, Q15, Q16, Q17: MJD122; DPAK
R7: 15k; 0204/5
R8: 5k; 0204/5
R9, R10, R33, R34: R-US_0204/5; 0204/5
R11, R14, R31: 2.2k; 0204/5
R12, R15, R32: 3k; 0204/5
R16, R17, R20, R21, R23, R26, R29: 1k; 0204/5
R25, R28: 2k; 0204/5
R27, R30: 1.5k; 0204/5
SJ1: SJW
SV1, SV2: MA03-1
SV3: FE08-1; FE08
SV4: MA07-1
U$1: DC-DC-STEP-DOWN-LM2596
X1: F37HP

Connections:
5V: ARDUINO_NANO1.12 (5V), IC6.14 (VCC), IC7.16 (VCC), IC8.8 (VCC), IC9.8 (V+), IC10.8 (V+), R10.1, R12.2, R15.2, R32.2, R34.1, SV1.3, SV2.3, SV3.8, U$1.OUT+, X1.20, X1.21, X1.22, X1.24, X1.25, X1.27, X1.29
A: ARDUINO_NANO1.7 (ADC3/A3), IC7.11 (A)
A0: ARDUINO_NANO1.4 (ADC0/A0), IC7.3 (X)
ACC: D13.C, D15.C, D21.C, D23.C, D33.C, IC1.1 (VDD), R7.2, SV3.7, U$1.IN+, X1.1, X1.10, X1.19, X1.35
AIRIN: C10.1, R9.2, R10.2, X1.5
AIROUT: C11.1, D9.C, IC7.15 (X2), R9.1
B: ARDUINO_NANO1.6 (ADC2/A2), IC7.10 (B)
C: ARDUINO_NANO1.5 (ADC1/A1), IC7.9 (C)
CKPIN: SV1.2, X1.4
CKPOUT: ARDUINO_NANO1.20 (D2/INT0), SV2.2
CLK1: ARDUINO_NANO1.1 (SCK/D13), IC6.8 (CLK)
CLR1: ARDUINO_NANO1.29 (D11/MOSI), IC6.9 (CLR)
DATA: ARDUINO_NANO1.28 (D10/OC1B/!SS), IC6.1 (A), IC6.2 (B)
ECN1: D16.C, P1.5, Q11.4 (C)
ECN1L: ARDUINO_NANO1.23 (D5/T1), IC1.14 (I)
ECN2: D18.C, P1.6, Q13.4 (C)
ECN2L: ARDUINO_NANO1.26 (D8/CLK0), IC1.9 (I)
GNC/GLP_MODE: ARDUINO_NANO1.10 (ADC6/A6)
GND: ARDUINO_NANO1.14 (GND), ARDUINO_NANO1.19 (GND), C3.2, C4.2, C5.2, C6.2, C10.2, C11.2, C12.2, C13.2, C14.2, C15.2, C16.2, C17.2, C18.2, C19.2, D1.A, D4.A, D6.A, D7.A, D9.A, D10.A, D11.A, D12.A, D14.A, D16.A, D18.A, D20.A, D22.A, D25.A, D26.A, D27.A, D32.A, IC1.8 (VSS), IC6.7 (GND), IC7.6 (INH), IC7.7 (VEE), IC7.8 (GND), IC8.1 (A0), IC8.2 (A1), IC8.3 (A2), IC8.4 (GND), IC9.4 (V-), IC10.4 (V-), Q1.3 (E), Q3.3 (E), Q5.3 (E), Q7.3 (E), Q9.3 (E), Q10.3 (E), Q11.3 (E), Q13.3 (E), Q15.3 (E), Q16.3 (E), Q17.3 (E), R8.1, R26.2, R29.2, SJ1.2, SV1.1, SV2.1, SV3.1, SV3.2, U$1.IN-, U$1.OUT-, X1.15, X1.23, X1.26, X1.28, X1.30, X1.34
IAC_A: SV4.4, X1.13
IAC_B: SV4.3, X1.32
IAC_C: SV4.2, X1.14
IAC_D: SV4.1, X1.33
INY1: D1.C, P1.1, Q1.4 (C)
INY2: D4.C, P1.2, Q3.4 (C)
INY3: D6.C, P1.3, Q5.4 (C)
INY4: D7.C, P1.4, Q7.4 (C)
INYL1A: ARDUINO_NANO1.21 (D3/INT1), IC1.3 (I)
INYL2A: ARDUINO_NANO1.24 (D6/AIN0), IC1.7 (I)
INYL3A: ARDUINO_NANO1.25 (D7/AIN1), IC1.11 (I)
INYL4A: ARDUINO_NANO1.22 (D4/T0), IC1.5 (I)
LAMB0: R25.1, X1.7
LAMB0OUT: C17.1, IC7.1 (X4), IC9.1 (OUT), R27.2
LAMB1: R28.1, X1.6
LAMB1OUT: C19.1, IC7.5 (X5), IC10.1 (OUT), R30.2
LED1: X1.11
M1: IC6.10 (QE), SV3.6
M2: IC6.11 (QF), SV3.5
M3: IC6.12 (QG), SV3.4
M4: IC6.13 (QH), SV3.3
MAPIN: C5.1, R33.2, R34.2, X1.8
MAPOUT: C6.1, D26.C, IC7.2 (X6), R33.1
unnamed: C18.1, IC10.3 (+IN), R28.2
unnamed: IC1.2 (O), Q1.1 (B)
unnamed: IC1.6 (O), Q3.1 (B)
unnamed: Q9.1 (B), R16.2
unnamed: IC1.12 (O), Q5.1 (B)
unnamed: IC1.4 (O), Q7.1 (B)
unnamed: Q17.1 (B), R21.2
unnamed: Q10.1 (B), R17.2
unnamed: IC1.15 (O), Q11.1 (B)
unnamed: IC1.10 (O), Q13.1 (B)
unnamed: Q15.1 (B), R20.2
unnamed: Q16.1 (B), R23.2
unnamed: C16.1, IC9.3 (+IN), R25.2
unnamed: IC9.2 (-IN), R26.1, R27.1
unnamed: IC8.7 (WP), SJ1.1
unnamed: IC10.2 (-IN), R29.1, R30.1
PWM: ARDUINO_NANO1.27 (D9/OC1A), SV4.7
RL1: IC6.5 (QC), R16.1
RL1IN: D12.C, D13.A, Q9.4 (C), X1.36
RL2: IC6.4 (QB), R17.1
RL2IN: D14.C, D15.A, Q10.4 (C), X1.18
RL3: IC6.6 (QD), R20.1
RL3IN: D20.C, D21.A, Q15.4 (C), X1.17
RL4: IC6.3 (QA), R23.1
RL4IN: D22.C, D23.A, Q16.4 (C), X1.37
RL5: ARDUINO_NANO1.30 (D12/MISO), R21.1
RL5IN: D32.C, D33.A, Q17.4 (C), X1.16
SCL: ARDUINO_NANO1.9 (ADC5/SCL/A5), IC8.6 (SCL)
SDA: ARDUINO_NANO1.8 (ADC4/SDA/A4), IC8.5 (SDA)
TEMPIN: C14.1, R14.1, R15.1, X1.3
TEMPOUT: C15.1, D11.C, IC7.14 (X1), R14.2
TPS2OUT: C4.1, D25.C, IC7.4 (X7), R31.2
TPSIN: C12.1, R11.1, R12.1, X1.2
TPSIN2: C3.1, R31.1, R32.1, X1.9
TPSM_A: SV4.6, X1.12
TPSM_B: SV4.5, X1.31
TPSOUT: C13.1, D10.C, IC7.13 (X0), R11.2
VBAT: D27.C, IC7.12 (X3), R7.1, R8.2
VIN: ARDUINO_NANO1.15 (VIN)

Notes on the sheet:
relay bomba/inyeccion
relay GNC/GLP mode
relay sonda lambda
relay A/A
relay electro ventilador
Modulo de control de valvula IAC o mariposa motorizada



Board: 2 copper layers, 102.7 x 102.5 mm, 85 parts (9 on the bottom side), 78 nets.

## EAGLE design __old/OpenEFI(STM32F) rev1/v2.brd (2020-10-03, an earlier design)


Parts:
D10, D11, D18: 1N4148DO35-7; DO35-7
D27: 5.1v; ZDIO-5
IC8: 24AA08SN; SO-08
J1, J2: 1053141206; MOLEX_1053141206
LED1, LED2, LED3, LED4, LED5: LED3MM
PROG: MA04-1
Q2: BC548; TO92-EBC
R3, R9, R10, R11, R12, R14, R15: 1k; 0204/5
R7: 15k; 0204/5
R8: 5k; 0204/5
SJ1: SJW
SV1, SV2: MA03-1
SV3: FE08-1; FE08
SV4: MA07-1
U$2: STM32F103C8T6-MODULE
X1, X3: F15HP
X2: MINI-USB_4P-85-32004-10X; 85-32004-10X

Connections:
3V3: U$2.3.3V_1 (3.3V); also elsewhere on the board
5V: D10.A, SV1.3, SV2.3, SV3.8; also elsewhere on the board
5V1: D10.C, D11.C, D18.C, IC8.8 (VCC), LED1.A, LED2.A, LED3.A, LED4.A, LED5.A, U$2.5V
5V-USB: D11.A, X2.1
A: U$2.PB_1; also elsewhere on the board
A1: U$2.PA_0; also elsewhere on the board
ACC: R7.2, SV3.7; also elsewhere on the board
B: U$2.PB_0; also elsewhere on the board
C: U$2.PA_7; also elsewhere on the board
CKPIN: SV1.2
CKPOUT: SV2.2
D: U$2.PA_6; also elsewhere on the board
D+: U$2.PA_12, X2.3
D-: U$2.PA_11, X2.2
GND: D27.A, IC8.1 (A0), IC8.2 (A1), IC8.3 (A2), IC8.4 (GND), PROG.1, Q2.E, R8.1, SJ1.2, SV1.1, SV2.1, SV3.1, SV3.2, U$2.GND_1 (GND), U$2.GND_2 (GND), U$2.GND_3 (GND), X2.4; also elsewhere on the board
IAC_A: SV4.4
IAC_B: SV4.3
IAC_C: SV4.2
IAC_D: SV4.1
L1: R9.1
L2: R10.1
L3: R11.1
L4: R12.1
L5: R14.1, U$2.PA_5
LED1: Q2.C
LED1A: R3.1
M1: SV3.6; also elsewhere on the board
M2: SV3.5; also elsewhere on the board
M3: SV3.4; also elsewhere on the board
M4: SV3.3; also elsewhere on the board
MISO: U$2.PB_6
MOSI: U$2.PB_7
unnamed: LED1.K (C), R9.2
unnamed: LED2.K (C), R10.2
unnamed: Q2.B, R3.2
unnamed: LED3.K (C), R11.2
unnamed: LED4.K (C), R12.2
unnamed: LED5.K (C), R14.2
unnamed: IC8.7 (WP), SJ1.1
unnamed: D18.A, PROG.4
PWM: SV4.7
RL1IN: J1.1; also elsewhere on the board
RL2IN: J1.2; also elsewhere on the board
RL3IN: J1.3; also elsewhere on the board
RL4IN: J1.4; also elsewhere on the board
RL5IN: J1.5; also elsewhere on the board
RL6IN: J1.6; also elsewhere on the board
RX: PROG.3, U$2.PA_9
SCK: U$2.PB_5
SCL: IC8.6 (SCL), U$2.PB_10; also elsewhere on the board
SDA: IC8.5 (SDA), U$2.PB_11; also elsewhere on the board
SS: U$2.PB_4
TPSM_A: SV4.6
TPSM_B: SV4.5
TX: PROG.2, U$2.PA_10
VBAT: D27.C, R7.1, R8.2; also elsewhere on the board

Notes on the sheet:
Modulo de control de valvula IAC o mariposa motorizada
321194


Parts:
C1: 0.1uf; C025-025X050
D2: 5.1v; ZDIO-5
DISPLAY: MA04-1
F2: TE5
IC3: 4067D; SO24W
IC11, IC12: 74HC595D; SO16
P1: 39-30-06; 39-30-?06?
P3: 39-30-04; 39-30-?04?

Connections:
5V: DISPLAY.2, IC3.24 (VDD), IC11.16 (VCC), IC12.16 (VCC); also elsewhere on the board
A: IC3.10 (A); also elsewhere on the board
A0: IC3.1 (X); also elsewhere on the board
AOUT0: IC3.2 (X7); also elsewhere on the board
AOUT1: IC3.3 (X6); also elsewhere on the board
AOUT2: IC3.4 (X5); also elsewhere on the board
AOUT3: IC3.5 (X4); also elsewhere on the board
AOUT4: IC3.6 (X3); also elsewhere on the board
AOUT5: IC3.7 (X2); also elsewhere on the board
AOUT6: IC3.8 (X1); also elsewhere on the board
AOUT7: IC3.9 (X0); also elsewhere on the board
AUX1: IC3.20 (X11)
AUX2: IC3.19 (X12)
AUX3: IC3.18 (X13)
AUX4: IC3.17 (X14)
AUX5: IC3.16 (X15)
B: IC3.11 (B); also elsewhere on the board
C: IC3.14 (C); also elsewhere on the board
D: IC3.13 (D); also elsewhere on the board
EX1: IC12.1 (QB)
EX2: IC12.2 (QC)
EX3: IC12.3 (QD)
EX4: IC12.4 (QE)
EX5: IC12.5 (QF)
EX6: IC12.6 (QG)
EX7: IC12.7 (QH)
GNC/GLP_MODE: C1.1, D2.C
GND: C1.2, D2.A, DISPLAY.1, F2.1, IC3.12 (VSS), IC3.15 (INH), IC11.8 (GND), IC11.10 (SCL), IC11.13 (G), IC12.8 (GND), IC12.10 (SCL), IC12.13 (G), P3.1, P3.2, P3.3, P3.4; also elsewhere on the board
GND2: F2.2; also elsewhere on the board
INY1: P1.1; also elsewhere on the board
INY2: P1.2; also elsewhere on the board
INY3: P1.3; also elsewhere on the board
INY4: P1.4; also elsewhere on the board
INY5: P1.5; also elsewhere on the board
INY6: P1.6; also elsewhere on the board
LAMB0OUT: IC3.23 (X8); also elsewhere on the board
LAMB1OUT: IC3.22 (X9); also elsewhere on the board
M1: IC11.15 (QA); also elsewhere on the board
M2: IC11.1 (QB); also elsewhere on the board
M3: IC11.2 (QC); also elsewhere on the board
M4: IC11.3 (QD); also elsewhere on the board
unnamed: IC11.9 (QH*), IC12.14 (SER)
RCK: IC11.12 (RCK), IC12.12 (RCK)
RL1: IC11.4 (QE); also elsewhere on the board
RL2: IC11.5 (QF); also elsewhere on the board
RL3: IC11.6 (QG); also elsewhere on the board
RL4: IC11.7 (QH); also elsewhere on the board
RL5: IC12.15 (QA); also elsewhere on the board
SCK2: IC11.11 (SCK), IC12.11 (SCK)
SCL: DISPLAY.4; also elsewhere on the board
SDA: DISPLAY.3; also elsewhere on the board
SER: IC11.14 (SER)
VBAT: IC3.21 (X10); also elsewhere on the board

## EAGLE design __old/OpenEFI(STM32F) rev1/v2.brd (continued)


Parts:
D1, D4, D6, D7, D16, D25: BZY97; F126Z12
Q1, Q6, Q7, Q14, Q20, Q23: IRLZ44Z; TO220BH
Q3, Q8, Q11, Q18, Q21, Q24: BC548; TO92-EBC
Q5, Q12, Q13, Q19, Q22, Q25: BC558A; TO92-EBC
R31, R32, R33, R34, R43, R44, R45, R46, R47, R48, R49, R50: R-EU_0207/10; 0207/10

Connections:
ACC: Q3.C, Q8.C, Q11.C, Q18.C, Q21.C, Q24.C; also elsewhere on the board
GND: D1.A, D4.A, D6.A, D7.A, D16.A, D25.A, Q5.C, Q12.C, Q13.C, Q19.C, Q22.C, Q25.C; also elsewhere on the board
GND2: Q1.S, Q6.S, Q7.S, Q14.S, Q20.S, Q23.S; also elsewhere on the board
INY1: D25.C, Q6.D; also elsewhere on the board
INY2: D1.C, Q1.D; also elsewhere on the board
INY3: D4.C, Q7.D; also elsewhere on the board
INY4: D6.C, Q14.D; also elsewhere on the board
INY5: D7.C, Q20.D; also elsewhere on the board
INY6: D16.C, Q23.D; also elsewhere on the board
INYL1A: R31.2
INYL2A: R33.2
INYL3A: R43.2
INYL4A: R45.2
INYL5A: R47.2
INYL6A: R49.2
unnamed: Q11.B, Q12.B, R31.1
unnamed: Q11.E, Q12.E, R32.2
unnamed: Q3.B, Q5.B, R33.1
unnamed: Q6.G, R32.1
unnamed: Q3.E, Q5.E, R34.2
unnamed: Q1.G, R34.1
unnamed: Q8.B, Q13.B, R43.1
unnamed: Q8.E, Q13.E, R44.2
unnamed: Q7.G, R44.1
unnamed: Q18.B, Q19.B, R45.1
unnamed: Q18.E, Q19.E, R46.2
unnamed: Q14.G, R46.1
unnamed: Q21.B, Q22.B, R47.1
unnamed: Q21.E, Q22.E, R48.2
unnamed: Q20.G, R48.1
unnamed: Q24.B, Q25.B, R49.1
unnamed: Q24.E, Q25.E, R50.2
unnamed: Q23.G, R50.1


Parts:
D9, D12, D13, D14, D15, D20: 1N4446; DO35-10
IC2: LM358D; SO08
Q4, Q9, Q10, Q15, Q16, Q26: BD139; TO126AV
R1: 2k; 0204/5
R2, R16, R17, R20, R21, R23, R51: 1k; 0204/5

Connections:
3V3: IC2.8 (V+); also elsewhere on the board
A0: R1.1; also elsewhere on the board
A1: IC2.1 (OUT), IC2.2 (-IN); also elsewhere on the board
GND: D9.A, D12.A, D14.A, D15.A, D20.A, IC2.4 (V-), Q4.E, Q9.E, Q10.E, Q15.E, Q16.E, Q26.E, R2.1; also elsewhere on the board
unnamed: Q26.B, R16.2
unnamed: Q16.B, R21.2
unnamed: Q9.B, R17.2
unnamed: IC2.3 (+IN), R1.2, R2.2
unnamed: Q10.B, R20.2
unnamed: Q15.B, R23.2
unnamed: Q4.B, R51.2
RL1: R16.1; also elsewhere on the board
RL1IN: D9.C, Q26.C; also elsewhere on the board
RL2: R17.1; also elsewhere on the board
RL2IN: D12.C, Q9.C; also elsewhere on the board
RL3: R20.1; also elsewhere on the board
RL3IN: D13.C, Q10.C; also elsewhere on the board
RL4: R23.1; also elsewhere on the board
RL4IN: D14.C, Q15.C; also elsewhere on the board
RL5: R21.1; also elsewhere on the board
RL5IN: D15.C, Q16.C; also elsewhere on the board
RL6: R51.1
RL6IN: D20.C, Q4.C; also elsewhere on the board

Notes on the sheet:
relay bomba/inyeccion
relay GNC/GLP mode
relay sonda lambda
relay A/A
relay electro ventilador


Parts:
C2, C8, C20, C22, C24, C26, C28, C30: 0.001uF; C025-025X050
C7, C9, C21, C23, C25, C27, C29, C31: C-EU025-025X050; C025-025X050
C16, C18: 0.001uf; C025-025X050
C17, C19: 0.22uf; C025-025X050
D3, D5, D8, D17, D19, D24, D28, D29: 5.1v; ZDIO-5
IC9: LM358D; SO08
R4, R5, R6, R13, R18, R19, R22, R24, R35, R36, R37, R38, R39, R40, R41, R42: R-US_0204/5; 0204/5
R25, R28: 2k; 0204/5
R26, R29: 1k; 0204/5
R27, R30: 1.5k; 0204/5

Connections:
5V: IC9.8 (V+), R5.1, R13.1, R19.1, R24.1, R36.1, R38.1, R40.1, R42.1; also elsewhere on the board
AIN0: C2.1, R4.2, R5.2
AIN1: C8.1, R6.2, R13.2
AIN2: C24.1, R35.2, R36.2
AIN3: C20.1, R18.2, R19.2
AIN4: C22.1, R22.2, R24.2
AIN5: C26.1, R37.2, R38.2
AIN6: C28.1, R39.2, R40.2
AIN7: C30.1, R41.2, R42.2
AOUT0: C7.1, D3.C, R4.1; also elsewhere on the board
AOUT1: C9.1, D5.C, R6.1; also elsewhere on the board
AOUT2: C25.1, D19.C, R35.1; also elsewhere on the board
AOUT3: C21.1, D8.C, R18.1; also elsewhere on the board
AOUT4: C23.1, D17.C, R22.1; also elsewhere on the board
AOUT5: C27.1, D24.C, R37.1; also elsewhere on the board
AOUT6: C29.1, D28.C, R39.1; also elsewhere on the board
AOUT7: C31.1, D29.C, R41.1; also elsewhere on the board
GND: C2.2, C7.2, C8.2, C9.2, C16.2, C17.2, C18.2, C19.2, C20.2, C21.2, C22.2, C23.2, C24.2, C25.2, C26.2, C27.2, C28.2, C29.2, C30.2, C31.2, D3.A, D5.A, D8.A, D17.A, D19.A, D24.A, D28.A, D29.A, IC9.4 (V-), R26.2, R29.2; also elsewhere on the board
LAMB0: R25.1
LAMB0OUT: C17.1, IC9.1 (OUT), R27.2; also elsewhere on the board
LAMB1: R28.1
LAMB1OUT: C19.1, IC9.7 (OUT), R30.2; also elsewhere on the board
unnamed: C18.1, IC9.5 (+IN), R28.2
unnamed: C16.1, IC9.3 (+IN), R25.2
unnamed: IC9.2 (-IN), R26.1, R27.1
unnamed: IC9.6 (-IN), R29.1, R30.1



Board: 2 copper layers, 149.9 x 148.8 mm, 149 parts (3 on the bottom side), 101 nets.

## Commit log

2019-04-16 agregado de placas ya existentes
    [module_CKP_Hall.brd, module_CKP_Hall.sch, module_CKP_Inductivo.sch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]
2019-04-19 Variante nueva!!
    Nueva variente de la placa basada en STM32F, se agrego un AtMega328 que va a correr una version modificada de OpenEFI para manejar las salidas e inyectores, ademas se agregaron mas pines de E/S se ca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
    [module_CKP_Hall.brd, module_CKP_Hall.sch, module_CKP_Inductivo.sch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]
2019-04-27 Creacion de V2 del PCB para SMT32F
    [v2.brd, v2.sch]
2019-04-29 cambios menores
    [v2.brd, v2.sch]
2019-04-30 Avances en I/O en rev1
    [v2.brd, v2.sch]
2020-10-03 init v3
    [Drivers.sch, Fuente.sch, IO_Principal.sch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]
2020-10-12 WIP v3 on STM32
    [Drivers.sch, STM32F rev3.kicad_pcb, STM32F rev3.sch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]
2020-11-08 V3 WIP
    [Drivers.sch, STM32F rev3.kicad_pcb, STM32F rev3.sch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]
2020-11-08 sacando porquerias
    [STM32F rev3.kicad_pcb]
2020-11-08 el ci ameo'
    [STM32F rev3.kicad_pcb]
2020-11-08 los espacios me dan ansiedad
    [Drivers.sch, STM32F_rev3.kicad_pcb, STM32F_rev3.sch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]
2020-11-08 update paths
    [STM32F_rev3.kicad_pcb, STM32F_rev3.sch]
2020-11-08 fix drc error
    [file5F54B133.sch]
2020-11-14 WIP V3
    [Drivers.kicad_sch, Drivers.sch, STM32F_rev3.kicad_pcb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]
2020-11-26 Update on PMIC
    [Drivers.kicad_sch, STM32F_rev3.kicad_pcb, STM32F_rev3.kicad_sch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]
2020-12-27 WIP: PAP Driver
    [Drivers.kicad_sch, STM32F_rev3.kicad_pcb, STM32F_rev3.kicad_sch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]
2021-04-01 Last commit to rev3
    [Drivers.kicad_sch, STM32F_rev3.kicad_pcb, STM32F_rev3.kicad_sch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]
2021-04-08 uEFI v2.x
    [Drivers.kicad_sch, Drivers.sch, SensorsV1.step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]
2021-04-10 Making sensor board easier to assemble
    [Sensors_V2.kicad_pcb]
2021-04-21 uEFI v2 beta release
    [Drivers.kicad_sch, connector.kicad_sch, file5F54B133.kicad_sch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]
2022-01-10 bump to kicad 6, init uEFI v3
    [Drivers.kicad_sch, Sensors_V2.kicad_pcb, Sensors_V2.kicad_sch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]
2022-02-05 move old boards to __old
    [Drivers.kicad_sch, Drivers.sch, Fuente.sch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]
2022-02-06 minor update
    [Drivers.kicad_sch, connector.kicad_sch, file5F54B133.kicad_sch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]
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2022-02-12 rev3, analog inputs
    [Drivers.kicad_sch, Sensors_V2.kicad_sch, file5F54B133.kicad_sch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]
2022-02-13 rev3 ADC SPI
    [file5F54B133.kicad_sch, uEFI_rev3.kicad_pcb, uEFI_rev3.kicad_sch]
2022-02-13 rev3, connect PMIC to injector outs
    [Drivers.kicad_sch, uEFI_rev3.kicad_pcb]
2022-02-18 rev3, PMIC, Relays done
    [file5F54B133.kicad_sch, uEFI_rev3.kicad_pcb, uEFI_rev3.kicad_sch]
2022-02-18 rev3, jtag
    [connector.kicad_sch, file5F54B133.kicad_sch, uEFI_rev3.kicad_pcb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]
2022-02-18 rev3, complete routing, ERC
    [uEFI_rev3.kicad_pcb, uEFI_rev3.kicad_sch]
2022-02-19 rev3, added acc detect
    [uEFI_rev3.kicad_pcb, uEFI_rev3.kicad_sch]
2022-03-03 fix 10k res
    [connector.kicad_sch, uEFI_rev3.kicad_pcb, uEFI_rev3.kicad_sch]
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2022-03-30 added actions, update old files to kicad 6
    [Drivers.sch, connector.sch, file5F54B133.sch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]
2022-03-30 branding, fix memory footprint
    [Drivers.kicad_sch, connector.kicad_sch, file5F54B133.kicad_sch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]
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2022-03-30 fix date/version
    [uEFI_rev3.kicad_pcb]
2022-03-30 revert date autofill
    [uEFI_rev3.kicad_pcb]
2022-05-01 uEFI rev 3.1.0
    [connector.kicad_sch, file5F54B133.kicad_sch, uEFI_rev3.kicad_pcb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]
2022-05-05 wip v3.1
    [connector.kicad_sch, uEFI_rev3.kicad_pcb, uEFI_rev3.kicad_sch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]
2022-05-07 Added connector for uEFI
    [uEFI_rev3.kicad_pcb, uEFI_v3.FCStd]
2022-09-24 add ckp sensor setup
    [connector.kicad_sch, file5F54B133.kicad_sch, uEFI_rev3.kicad_pcb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]
2022-09-27 uEFI rev 3.1
    [uEFI_rev3.kicad_pcb]
2022-09-29 uEFI r3.2
    [file5F54B133.kicad_sch, uEFI_rev3.kicad_pcb, uEFI_rev3.kicad_sch]
2022-10-12 uEFI rev 3.3
    [uEFI_rev3-B_Cu.gbl, uEFI_rev3-B_Paste.gbp, uEFI_rev3-B_Silkscreen.gbo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]
2022-10-25 pre-production files, uEFI v3.4
    [connector.kicad_sch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]
2022-11-12 fix bom output
    [file5F54B133.kicad_sch, pwm_relays.kicad_sch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]
2023-01-19 AA wiring, lib&connector update, added eggbug
    [AC.kicad_sch, connector.kicad_sch, uEFI_rev3.kicad_pcb]
2023-01-23 Fix SPI pad & connector, add new images, Co-authored-by: Lucacik <name@example.com>
    [uEFI_rev3-CuBottom.gbr, uEFI_rev3-CuIn1.gbr, uEFI_rev3-CuIn2.gbr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]
2023-03-04 fix relay tracks
    [uEFI_rev3.kicad_pcb]
2023-07-01 uEFI v3, fix 12v => 5v overcurrent issue
    [Drivers.kicad_sch, connector.kicad_sch, file5F54B133.kicad_sch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]
2023-10-07 rev4 init
    [AC.kicad_sch, Drivers.kicad_sch, SensorsV1.step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]
2023-10-07 import PCB outline from rusEFI / hellen board
    [connector.kicad_sch, uEFI_rev3.kicad_pcb]
2023-10-09 wip PMIC on rev4 board
    [PMIC.kicad_sch, file5F54B133.kicad_sch, pwm_relays.kicad_sch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]
2023-10-13 changes on sensors sch
    [OpenEFI_rev4.kicad_pcb, OpenEFI_rev4.kicad_sch, PMIC.kicad_sch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]
2023-10-14 wip sensors pinout:
    [A4988_STEPPER_MOTOR_DRIVER_CARRIER.step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]
2023-10-14 update sensors/connector pinout, added rtc vbatt backup
    [OpenEFI_rev4.kicad_sch, PMIC.kicad_sch, connector.kicad_sch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]
2023-10-19 WIP Analog frontend
    [DLW21SZ900HQ2L.step, Drivers.kicad_sch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]
2023-10-19 WIP analog frontend, init ckp"
    [OpenEFI_rev4.kicad_sch, connector.kicad_sch]
2023-10-20 WIP relay driver
    [connector.kicad_sch, untitled.kicad_sch]
2023-10-22 WIP CKP/CMP
    [PMIC.kicad_sch, connector.kicad_sch]
2023-10-22 fix board errors
    [OpenEFI_rev4.kicad_sch, connector.kicad_sch, file5F54B133.kicad_sch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]
2023-10-22 add tacho driver
    [OpenEFI_rev4.kicad_sch]
2023-10-23 wip SD card
    [104031-0811.step, OpenEFI_rev4.kicad_sch, connector.kicad_sch]
2023-10-28 wip relay pcb
    [54-00025--3DModel-STEP-510211.STEP, OpenEFI_rev4.kicad_sch]
2023-11-01 WIP SPI
    [OpenEFI_rev4.kicad_sch]
2023-11-02 fix pcb size/wideband
    [OpenEFI_rev4.kicad_sch]
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2023-11-11 Rev4: add all MCU signals
    [OpenEFI_rev4.kicad_sch, PMIC.kicad_sch, connector.kicad_sch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]
2023-11-12 Rev4 WIP LCSC assigments
    [OpenEFI_rev4-CuBottom.gbr, OpenEFI_rev4-CuIn1.gbr, OpenEFI_rev4-CuIn2.gbr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]
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

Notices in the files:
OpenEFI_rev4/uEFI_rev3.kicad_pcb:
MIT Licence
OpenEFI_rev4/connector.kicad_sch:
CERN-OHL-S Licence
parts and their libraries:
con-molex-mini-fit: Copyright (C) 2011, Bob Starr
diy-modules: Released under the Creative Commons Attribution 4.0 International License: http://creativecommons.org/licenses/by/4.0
